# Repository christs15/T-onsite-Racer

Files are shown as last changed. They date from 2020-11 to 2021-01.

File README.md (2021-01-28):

# T-onsite-Racer 

Workshop Documentation for T-onsite Racer @ CMD+O



## Respository structure

**root directory:** Building instruction and programming instructions to build T-onsite-Racer.

**Groupwork**: Introdcution to Bluetooth Low Energy and Microcontroller.

**CAD::** T-Racer CAD Files.

**Arduino:** Template sketch as "programming guide" for the T-Racer and sample solution.

**App:** Link and introdcution to download the T-Racer app directly from AppStore/PlayStore to controll your car. For Android there is an prebuild apk. You can also find the source code of the app in the subdirectory "sources".

**images:** Pictures and impressions of the T-Racer.

## App

We have a prebuild IOS and Android app, which can be officially downloaded as a trial version in the respective stores. You can find the link to the app for your platform in the app subfolder.

You can also find the source code here. So you can build your app for the corresponding platform. The app is implemented in ionic and can be built for both, android and ios. First the development/build environment has to be configured accordingly:

1. Clone this repo
2. Install Node.js current version (https://nodejs.org/en/download/)
3. Install the Ionic CLI with npm in CMD - npm install -g @ionic/cli (https://ionicframework.com/docs/intro/cli)
4. Download Android SDK and JDK8 (https://ionicframework.com/docs/developing/android)
5. Download Gradle and set Path to System (https://gradle.org/install/)
6. Use IDE for modifications: example (Visual Studio Code - https://code.visualstudio.com/)
7. In project directory, install nippljs - npm i nipplejs (https://www.npmjs.com/package/nipplejs)

How to deploy on android device:
Note: Compatible with Android 5.2 and higher.

1. In project directory, run - ionic cordova prepare android (https://ionicframework.com/docs/cli/commands/cordova-prepare)
2.  In project directory, run - ionic cordova run android -1 (to deploy on android Phone: https://ionicframework.com/docs/cli/commands/cordova-run)

Visit "https://ionicframework.com/docs" for complete documentation.

## T-Racer "tuning"

To make the T-Racer a bit faster, you can buy a new engine, for example with 900rpm. Make sure that the dimensions are correct, otherwise it won't fit into the provided holder.

You can also turn up the step-up converter to 10-12V to get the maximum power out of your motor. 
Attention: The servo motor has an operating voltage of 5V. According to the wiring diagram, the servo is connected to the output of the step-up. If the step-up is turned up to over 5V, the servo must be replugged. You can then connect the servo motor directly to the battery.

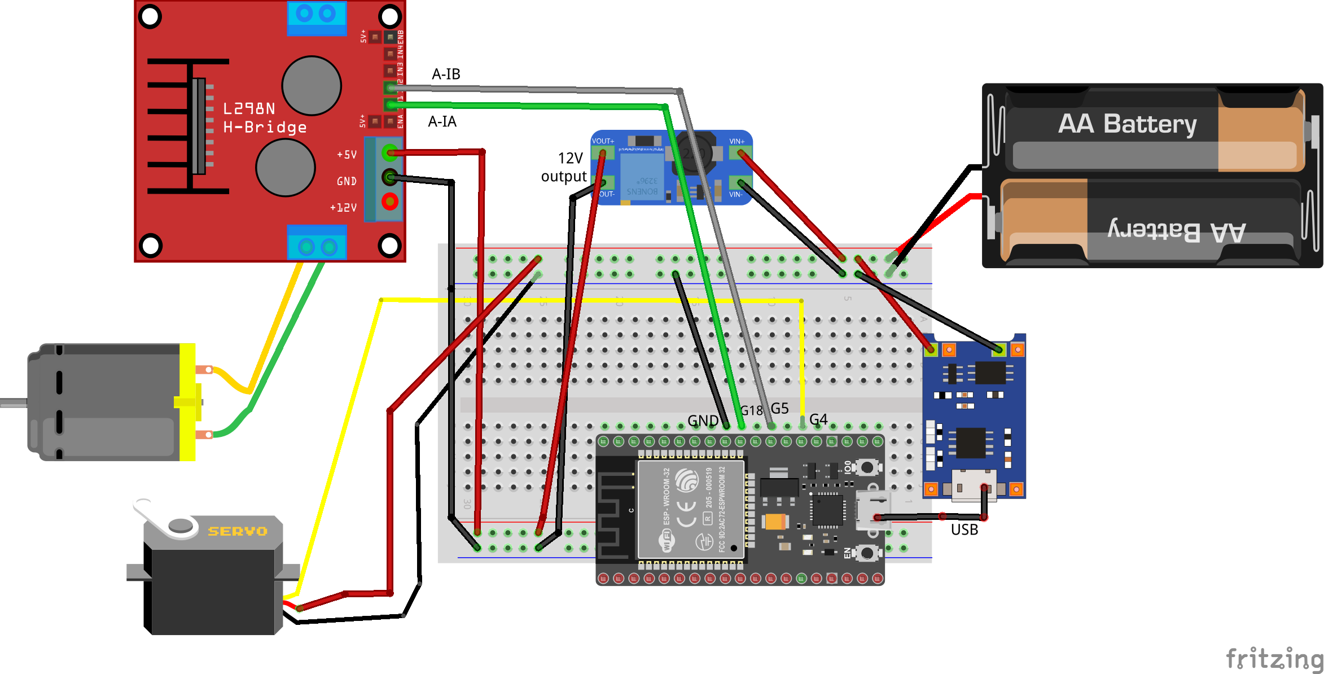
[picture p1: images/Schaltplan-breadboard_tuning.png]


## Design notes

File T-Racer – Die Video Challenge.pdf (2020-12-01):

# T-Racer – Die Video Challenge

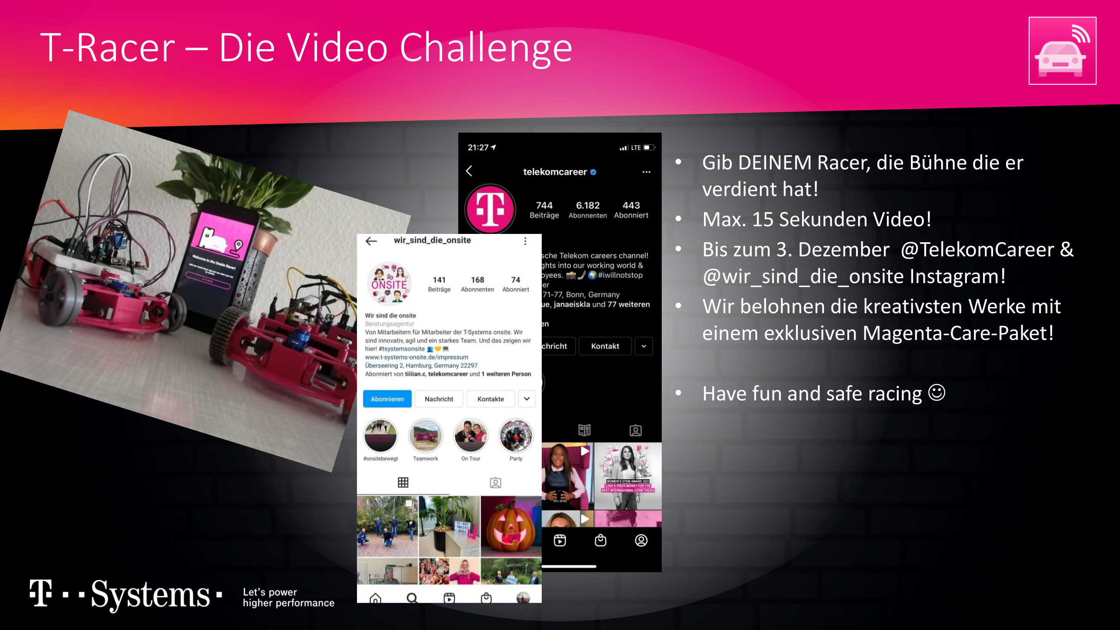
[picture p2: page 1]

- Gib DEINEM Racer, die Bühne die er verdient hat!
- Max. 15 Sekunden Video!
- Bis zum 3. Dezember @TelekomCareer & @wir_sind_die_onsite Instagram!
- Wir belohnen die kreativsten Werke mit einem exklusiven Magenta-Care-Paket!
- Have fun and safe racing ☺

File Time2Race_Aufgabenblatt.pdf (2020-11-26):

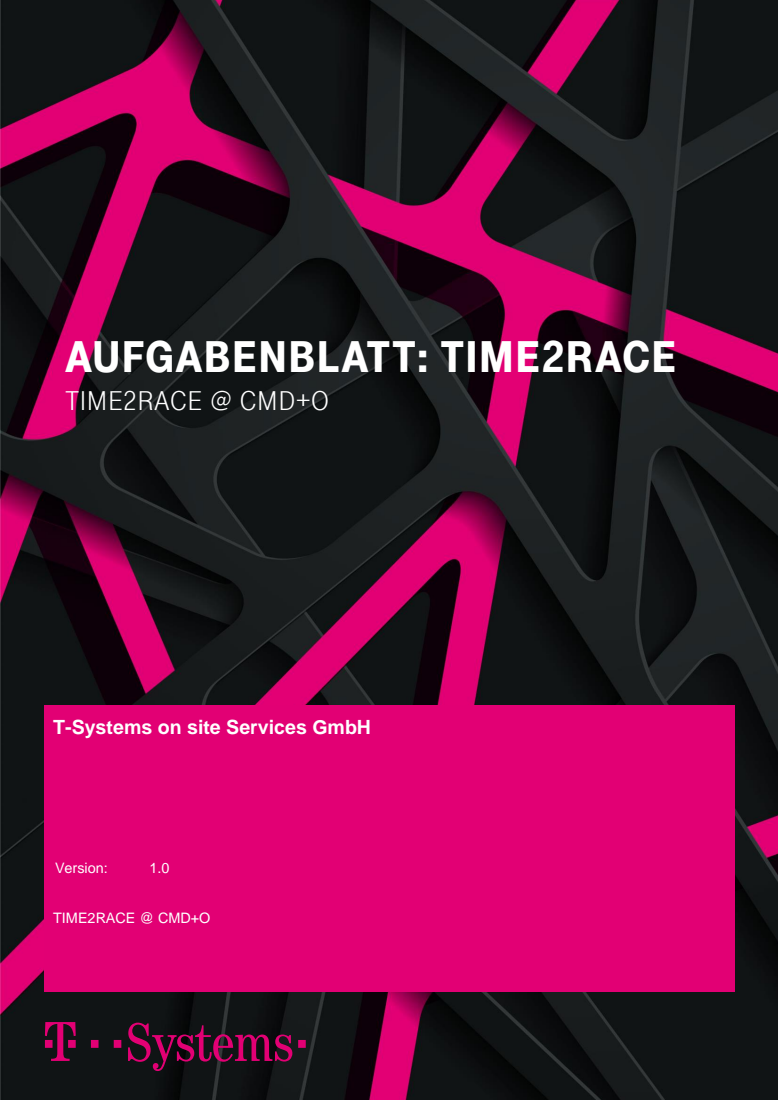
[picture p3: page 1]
AUFGABENBLATT: TIME2RACE; TIME2RACE @ CMD+O; Version:

T-Systems on site Services GmbH

T-SYSTEMS ON SITE SERVICES GMBH | Seite 2 von 20
Innovation Lab T-Systems onsite West | Version:1.0

TIME2RACE Aufgabenblatt

## IMPRESSUM

Herausgeber | T-Systems on site Services GmbH
| Fasanenweg 5 70771 Leinfelden-Echterdingen
Version | Letztes Review
1.00 | 20.11.2020

Kurzbeschreibung
Anweisung und Hilfestellung zur Umsetzung des T-Racers

Copyright © 20.11.2020 by T-Systems on site Services GmbH

Alle Rechte, auch die des auszugsweisen Nachdrucks, der fotomechanischen Wiedergabe (einschließlich Mikrokopie) sowie der Auswertung durch Datenbanken oder ähnliche Einrichtungen, vorbehalten.

## Inhaltsverzeichnis

## Abbildungsverzeichnis

1 | T-RACER
1.1 | Was ist zu tun?

Ziel dieses Workshops ist das Entwickeln deines eigenen T-Racers, welcher per Bluetooth Low Energy steuerbar ist. Das Herzstück des T-Racers ist ein ESP32 Dev Board, welches du über die Arduino IDE programmieren kannst. Darüber steuerst du den Motor für den Antrieb, sowie den Servo Motor für die Lenkung. Für die Kommunikation zwischen App und T-Racer wird das Protokoll Bluetooth Low Energy eingesetzt.

1.2 | Die Macht der Schaltung

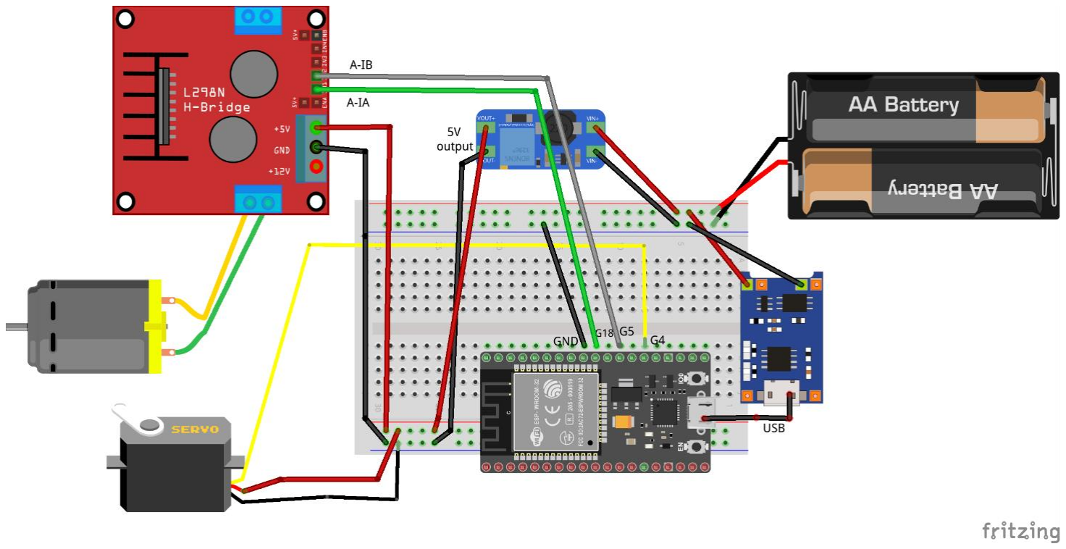
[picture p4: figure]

Abbildung 1: Schematischer Schaltplan

## 1.2.1 Hardware Komponenten

ESP 32

Step up (MT3608)

Der ESP32 ist eine kostengünstige und mit geringem Leistungsbedarf ausgeführte 32-Bit-Mikrocontrollerfamilie der Firma espressif. Er kommt standardmäßig mit Wifi und BLE an Bord.

Der MT3608 ist ein Step-Up Konverter (Auswärtswandler). Dieser wird benötigt, um die Spannung der Batterie auf konstante 5V zu regeln.

Eingangsspannung: 2V - 24V, Ausgangsspannung: bis 28V, Max Nennstrom: 2A

Power supply Modul

AA-Batterien

Servo Motor

DC Getriebe
Motor

L9110 Motor
controller

Breadboard

WICHTIG: Wenn der T-Racer nicht verwendet wird, sollte der Akku entfernt werden!

Wird benötigt, um die 4,5 Volt des Akkus auf konstante 5 Volt zu bringen, so kommt es nicht zu Verbindungsabbrüchen des BLE Chips. Der Spannungswandler verfügt über einen USB Output, wodurch eine einfache Stromversorgung des ESP32 ermöglicht wird.

3x 1,5V für die Stromversorgung

Servo Motor für die Lenkung des T-Racers.

DC Motor mit vorgeschaltener Getriebebox für den Antrieb. Durch die Getriebeübersetzung liefert der Motor genug Drehmoment, um den T-Racer zu bewegen. Max 300 rpm.

L9110 H-Bridge zum steuern des DC Motors. Mit dem L9110 können bis zu 2 Motoren angesteuert werden. Dieser ist erforderlich, um die Motorrichtung umkehren zu können. Mit einem einfachen MOS-FET können wir nur die Leistung ändern, aber nicht die Richtung.

Steckplatine für einfaches Prototyping.

2 | SETUP
2.1 | Ein Ausflug in die Bibliotheken

Um den Programmcode für unsere Christbaumkugel zu schreiben werden einige externe Bibliotheken benötigt, welche mittels „include“ eingebunden werden müssen.
Folgende Bibliotheken sind bereits durch Arduino selbst oder durch das „esp32“-Paket mitgeliefert:
- ESP_WiFi: (Optional) Stellt allgemeine Funktionen für WiFi-Verbindungen zu Verfügung. Wir benötigen
| sie aber nur um WiFi abzuschalten, damit der Stromverbrauch reduziert wird.
- BLEDevice: Klasse für ein BLE Device. Die Grundlage für die BLE Kommunikation.
- BLEServer: Klasse für einen BLE Server. Hierauf kann sich später das Smartphone verbinden.
- BLEUtils: Allgemeine Funktionen für BLE.
- ESP32Servo: Bibliothek für die Kommunikation mit dem Servo Motor
2.2 | Genau die richtige Debugging App für den T-Racer – nRFConnect

Um die Bluetooth-Verbindung von Smartphone aus zu testen kann die App nRFConnect genutzt werden. Die App ist für Android sowie iOS kostenlos verfügbar:
- https://play.google.com/store/apps/details?id=no.nordicsemi.android.mcp&hl=en_US
- https://apps.apple.com/us/app/nrf-connect/id1054362403
2.3 | Arduino - Was sonst?

Um das Board über euren Computer zu programmiere, müsst ihr es per Mikro-USB anschließen. Das Board wird über einen virtuellen COM Port angesprochen. Hierzu benötigt der Computer noch die passenden Treiber. Diese sind hier zu finden:
https://www.silabs.com/products/development-tools/software/usb-to-uart-bridge-vcp-drivers
Anschließend kann man sich die Arduino IDE unter https://www.arduino.cc/ für alle gängigen Betriebssysteme downloaden und installieren. Zunächst ist es wichtig, alle benötigten Boardkonfigurationen und Bibliotheken einzubinden, um den ESP32 über die IDE nutzen zu können. Dazu geht man unter „Datei -> Voreinstellungen“ und fügt eine „zusätzliche Boardverwalter-URL“ ein: https://dl.espressif.com/dl/package_esp32_index.json

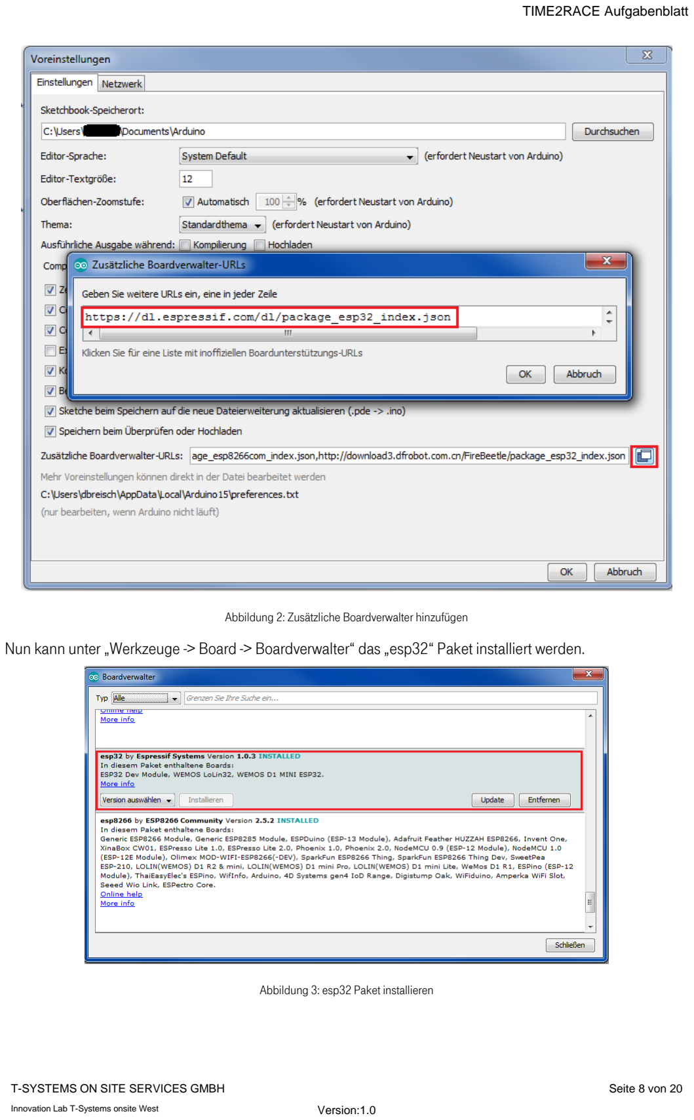
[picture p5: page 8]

Abbildung 2: Zusätzliche Boardverwalter hinzufügen
Nun kann unter „Werkzeuge -> Board -> Boardverwalter“ das „esp32“ Paket installiert werden.

Abbildung 3: esp32 Paket installieren

Damit nun die IDE weiß für welches Board tatsächlich entwickelt wird, gibt man abschließend unter „Werkzeuge“ die korrekte Konfiguration wie in Abbildung 4 dargestellt an. Wichtig hierbei ist zudem das Auswählen des richtigen virtuelle COM Ports, an dem das Board angeschlossen ist.

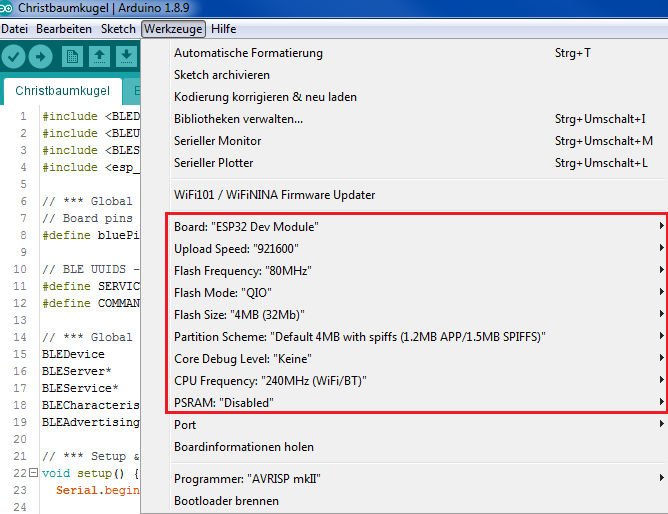
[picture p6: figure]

Abbildung 4: Boardkonfiguration
Will man den Sketch auf das Board flashen, klickt man auf den Pfeil „Hochladen“ (oben links in der IDE). Daraufhin wird der Sketch kompiliert und das Flashen beginnt. Will man lediglich kompilieren, klickt man auf den Haken „Überprüfen“.
Während des Flashvorgangs wird am unteren Bildschirm der aktuelle Vorgang in der Konsole ausgegeben. Sobald dort „Connecting…“ steht, muss in einigen Fällen der „Boot“ Knopf des Boards gedrückt werden, bis die Übertragung startet. Danach kann der Knopf losgelassen werden.

Abbildung 5: Konsolenausgabe beim Flashen
Eine praktische Debugmöglichkeit bietet der „Serielle Monitor“, der in der rechten oberen Ecke zu finden ist. Hier werden alle seriellen Ausgaben des Controllers angezeigt, die der Entwickler erstellt hat.

Abbildung 6: Button "Serieller Monitor"

Für Linux Nutzer:
Unter Linux muss zunächst die Versionskontrollsoftware Git und das Python-Modul Serial mittels

sudo apt install git python-serial

installiert werden.

Damit nun die IDE weiß für welches Board tatsächlich entwickelt wird, gibt man abschließend unter „Werkzeuge“ die korrekte Konfiguration wie in Abbildung 4 dargestellt an. Wichtig hierbei ist zudem das Auswählen des richtigen virtuelle COM Ports, an dem das Board angeschlossen ist.

2.4 | Sag Hallo, zur Welt!

Zum Testen der Konfiguration kann ein kleiner „Hello-World“ Sketch implementiert werden. Hierzu muss über „Datei -> Neu“ ein neuer Sketch angelegt werden. Mithilfe des in Abbildung 7 dargestelltem Sketch kann eine Serielle Ausgabe geschrieben werden, welche im Seriellen Monitor verfolgt werden kann. Dabei ist darauf zu achten, dass die Baudrate im Seriellen Monitor mit der im Sketch hinterlegten Baudrate (115200) übereinstimmt.

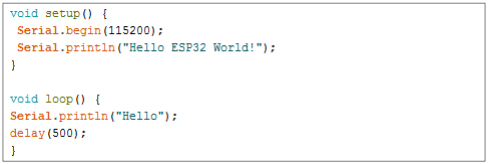
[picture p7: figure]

Abbildung 7 Hello World Sketch
2.5 | Warum löten, wenn man stecken kann?

Ein Breadboard (Steckplatine) ermöglicht es, schnell und einfach Schaltungen zu testen, ohne das gelötet werden muss.

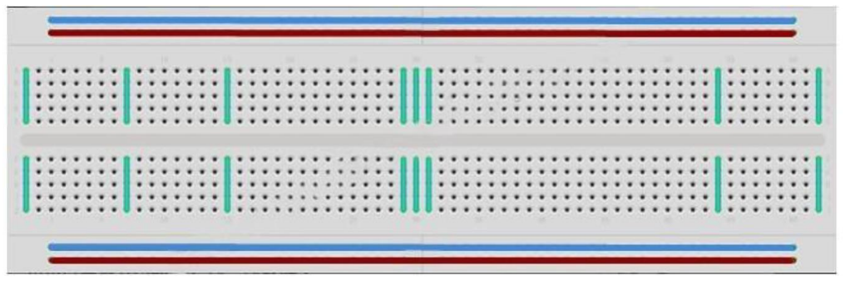
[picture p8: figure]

Abbildung 8 Breadboard

Innerhalb des Breadboards befinden sich Metallstreifen, welche die elektrische Verbindung zwischen den Kontaktstellen herstellen. Dabei sind immer die Kontakte innerhalb derselben Reihe (grün eingezeichnet) miteinander verbunden. Wenn du die Pins zweier Bauteile in dieselbe Kontaktreihe steckst, sind diese also miteinander verbunden. Zudem gibt es zwei „Powerlines“ (Rails), welche für die Stromversorgung genutzt werden.

3 | PROGRAM YOUR RACER
3.1 | Find the right way: Lenkung

Angeschlossen wird der Servo über ein dreipoliges Kabel. Dabei handelt es sich um zwei Versorgungsleitungen
- VCC (rot) und GND (braun), sowie eine Datenleitung (gelb).
Mit dem Servo wird eine Winkelbewegung zwischen 0 und 180 Grad gesteuert. Die Neutralposition ist dabei bei 90 Grad erreicht, während 0 und 180 Grad jeweils den Linken und Rechten Anschlag definieren. Bedeutet also, dass wenn du die Servo auf 90 Grad stellst, fährt dein T-Racer geradeaus.
Zur Ansteuerung des Servomotors werden wir die Servo-Klasse aus der Arduino-Servobibliothek " ESP32Servo.h " verwenden.

Beispiel:

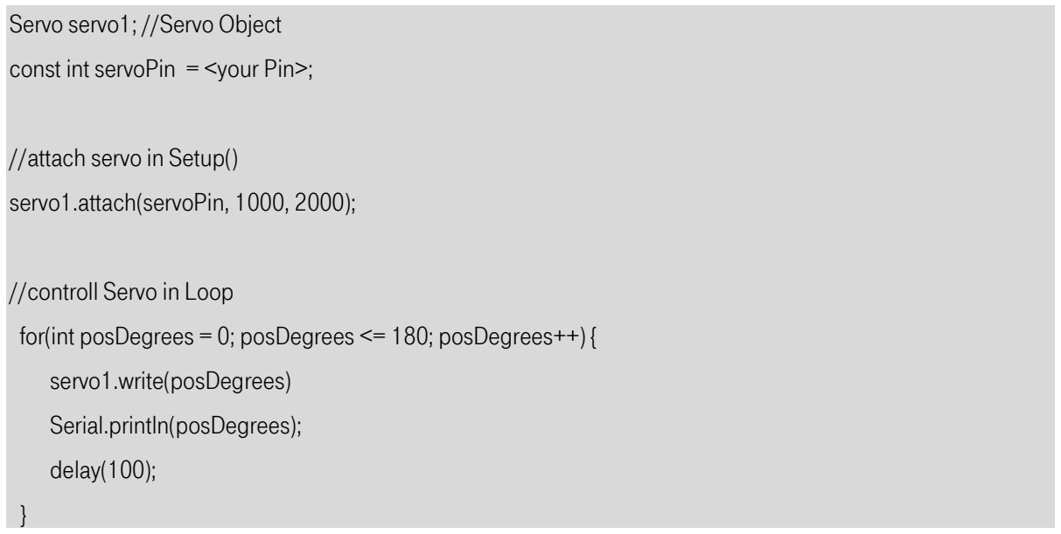
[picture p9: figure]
Servo servo1; //Servo Object; const int servoPin = <your Pin>;; //attach servo in Setup(); servo1.attach(servoPin, 1000, 2000);; //controll Servo in Loop; servo1.write(posDegrees); Serial.println(posDegrees);; delay(100);

for(int posDegrees = 0; posDegrees <= 180; posDegrees++) {

3.2 | Start your motors: Antrieb

Die digitalen Pins auf dem Entwicklerboard haben eine konstante Ausgangsspannung von 5V bzw. 3.3V. Um die Spannung ändern zu können, unterstützen einige Pins ein PWM-Signal.
Mit dem PWM-Signal und einem MOS-FET können wir die an einen Gleichstrommotor gelieferte Leistung variieren, um so die Geschwindigkeit zu bestimmen. Dadurch könnte die Leistung des Motors angepasst werden, allerdings kann so die Richtung nicht geändert werden. Um die Richtung zu ändern, muss die Polarität getauscht werden, hierzu wird die H-Bridge benötigt.
Motor Variablen definieren:
//motor Pins
int motorDir = 18; // → INA int motorPWM = 5; // → INB

MotorDIR: Richtung des Motors bestimmen (LOW oder HIGH) für Rückwerts oder Vorwärts.
MotorPWM: Drehzahl des Motors bestimmen (Geschwindigkeit) – LOW oder HIGH für volle Geschwindigkeit

Mithilfe der truth table, kann abgeleitet werden, wann der Motor rückwärts bzw. vorwärts fährt.

Table 1 truth table

IA | IB | Output
LO | LO | Off
HI | LO | Forward
LO | HI | Reverse
HI | HI | Off

Vorwärts:
- IA (motorDIR) auf HIGH setzen (5v)
- IB (motorPWM) 255 = Motor aus (siehe truth table), IB (motorPWM) 0 = volle Geschwindigkeit
- Die PWM-Zahl von IB kann nun angepasst werden, um die Leistung des Motors anzupassen → pow digitalWrite( motorDir, HIGH ); // direction = forward
analogWrite( motorPWM, pow );

Rückwärts:
- IA (motorDIR) auf LOW setzen (0v)
- IB (motorPWM) 0 = Motor aus (siehe truth table)
- IB = 255 = maximum power → pow digitalWrite( motorDir, LOW ); // direction = backwards analogWrite( motorPWM, pow );

Anhalten:
digitalWrite( motorDir, LOW ); // Set motor to off
digitalWrite( motorPWM, LOW );

Der Motor kann nun vorwärts und rückwärts betrieben werden indem jeweils die MotorDIR sowie der entsprechende PWM Wert (zwischen 0 und 255) gesetzt wird. Das heißt, wenn wir nur den Wert 0-255 senden, wissen wir nicht, ob der T-Racer vorwärts oder rückwärts fahren muss. Ein weiterer Wert, welcher diese Info enthält, müsste mitgesendet werden. Um dies zu umgehen, sendet die T-Racer App nur einen Wert von 0-255, wobei 128 Stillstand bedeutet. Ist der Wert größer als 128, sollte der T-Racer vorwärtsfahren, ist der Wert kleiner als 128, sollte der T-Racer rückwärtsfahren. Damit trotzdem das volle Spektrum des Motors genutzt werden kann, müssen die Werte entsprechend umgerechnet werden.

Vorwärts: pow = 255 - ((fb - 128) * 2);
Rückwärts: pow = 255 - (fb * 2);

Achtung: Wie rum du deinen Motor an der H-Bridge anschließt ist wichtig, um später beim Vorwärtsfahren, auch wirklich nach vorne zu fahren. Sollte dein Auto beim vorwärts Befehl, rückwärtsfahren, tausche einfach die Anschlüsse des Motors an der H-Bridge

3.3 | Connect to your T-Racer: BLE Verbindung initialisieren
1. Einbinden aller nötigen Bibliotheken
| Um die externen Bibliotheken nutzen zu können, müssen diese zu Beginn eingebunden werden.
| #include <BLEDevice.h> #include <BLEUtils.h> #include <BLEServer.h>
2. Variablen definieren
| Globale Variablen definieren:

…..
….
#define SERVICE_UUID "ae975c80-05f0-11ea-8d71-362b9e155667" #define COMMAND_CHAR_UUID "b81f189c-05f0-11ea-8d71-362b9e155667" BLEDevice Device;

BLEServer* pServer;
BLEService* pService;
BLECharacteristic* pControllCharacteristic; BLEAdvertising* pAdvertising;

setup{
….
….
}

loop{
…
….
}

Achtung: Achte darauf, dass die UUID´s übereinstimmen. Andernfalls kann die App deinen T-Racer nicht finden.

3. Bluetooth initialisieren
Um eine Verbindung mit dem Central einzugehen, muss zunächst das Bluetooth initialisiert werden. Dazu sind mehrere Schritte nötig.
a. Bluetooth Gerät erstellen
Zunächst muss das BLE Gerät initialisiert werden. Dabei kann der Name des Gerätes bestimmt werden.

Device.init("Name of BLE Device");

b. BLE Server erstellen
Nachdem das BLE Gerät erstellt wurde, muss dieses als BLE Server konfiguriert werden. pServer ist dabei vom Typ BLEServer:
pServer = Device.createServer();
c. Profil definieren

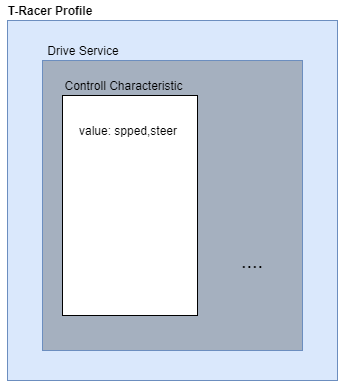
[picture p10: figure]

Abbildung 9 T-Racer Profile
void initBLE() {
….
…..
pService = pServer->createService(SERVICE_UUID);
pControllCharacteristic = pService->createCharacteristic(COMMAND_CHAR_UUID,
BLECharacteristic::PROPERTY_WRITE_NR | BLECharacteristic::PROPERTY_WRITE);
// has to be enabled for iOS pControllCharacteristic->setWriteNoResponseProperty(true);
//Callback Methoden
pServer->setCallbacks(new ServerCallbacks()); pControllCharacteristic ->setCallbacks(new CharacteristicCallbacks()); ….
…
}

d. UUIDs
Der Service sowie die Charakteristiken benötigen eine UUID, also eine einzigartige ID welche sie repräsentiert. Wie unter Aufgabenpunkt 2 werden dafür Präprozessor Konstanten angelegt. Diese werden direkt unter die oben angelegten Konstanten geschrieben. Damit BLE Client und BLE Server miteinander kommunizieren können, müssen beide das Profil implementieren. Der BLE Client (App) muss daher wissen in welche Charactersitic er die entsprechenden Werte schreiben muss. Um dies zu garantieren, müssen folgende UUIDs zugewiesen werden:

Drive ServiceUUID: "ae975c80-05f0-11ea-8d71-362b9e155667"
Controll CharacteristicUUID: "b81f189c-05f0-11ea-8d71-362b9e155667"
e. In den Advertising Zustand wechseln
Ist das Gerät initialisiert und das Profil definiert, kann der Service gestartet und in den Advertising Zustand gewechselt werden, sodass andere BLE Geräte das Gerät durch das Scannen der Umgebung finden können. Die nötigen Befehle können dem Cheat sheet entnommen werden. Anschließend versendet das Gerät Advertising Nachrichten mit der definierten Nachricht auf den dafür vorgesehen Advertising Kanälen. Durch das Scannen der Umgebung mithilfe der NRFConnect App, sollte das initialisierte Gerät nun sichtbar werden. Dazu muss der Sketch zunächst kompiliert und auf dem Mikrocontroller geflasht werden.
void initBLE {
…
…
//start_advertising
Device.startAdvertising(); Serial.println("Start Advertising"); }
3.4 | Control your T-Racer: Steuerung über BLE

Nachdem du dich erfolgreich mit deinem ESP32 verbinden kannst, wird es Zeit, die übertragenen Werte richtig zu empfangen und zu interpretieren.

1. Werte auf dem BLE-Server empfangen
Um den Wert der Charakteristik beim Empfangen eines neuen Wertes vom Client verarbeiten zu können, muss eine sogenannte Callback Methode definiert werden, welche aufgerufen wird, sobald ein Wert in die Charakteristik geschrieben wird.
Dazu muss zunächst die Callback initialisiert werden:

(Info: die Zeile habt ihr schon in der initBLE() Methode )

pCharCommand->setCallbacks(new CharacteristicCallbacks());

Anschließend kann über die Callback-Klasse der Wert ausgelesen werden, indem die Methode onWrite() überlagert wird.

class CharacteristicCallbacks: public BLECharacteristicCallbacks {
void onWrite(BLECharacteristic* pCharacteristic) {
//receive value via BLE from characteristic
std::string value = pCharacteristic->getValue();
//convert to String
String svalue= value.c_str();
}
};
2. Wert senden, empfangen und ausgeben
Um zu überprüfen, ob die gesendeten Werte richtig empfangen werden, eignet sich die App nRF Connect sehr gut. Damit kannst du dich mit deinem T-Racer verbinden und siehst anschließend das definierte BLE Profil.

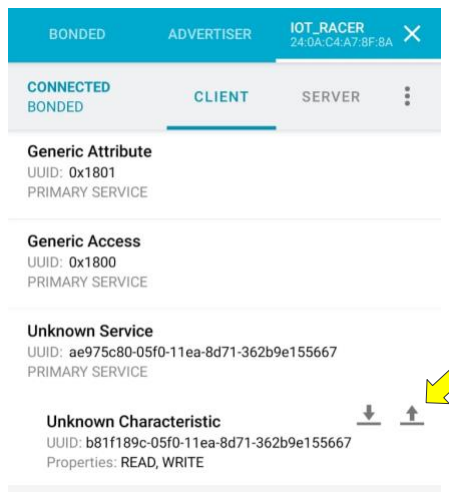
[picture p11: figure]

Um jetzt einen Wert zu senden, klicke auf den „write“-Pfeil und gebe einen Wert ein. Da serverseitig ein String erwartet wird, wähle UTF8 bzw. Text aus und klicke anschließend auf „send“. Danach solltest du den Wert im seriellen Monitor sehen können.

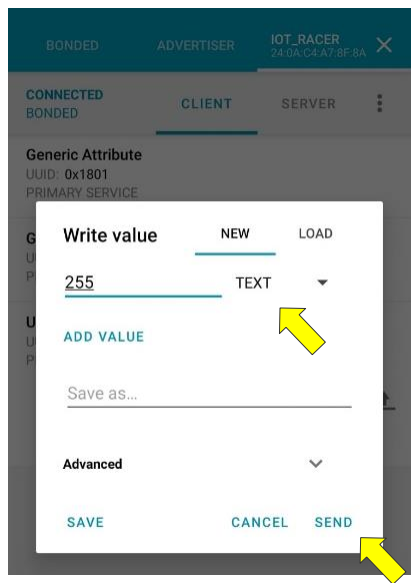
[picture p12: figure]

3. Werte interpretieren
Die T-Racer App sendet die Werte für die Lenkung und den Speed gebündelt in einer Charakteristik im folgenden Format: <speed,steer>
Daher müssen die Werte zuerst geparsed und dann an die Servo und den DC-Motor übergeben werden z. B über eine Methode carControll(speed, steer)

A | CHEATSHEET

Allgemein:

Serial.begin(9600) | Baudrate für die serielle Übertragung definieren.
Serial.println(“STRING“) Serial.print(“STRING“) | Gibt STRING auf dem seriellen Monitor aus. Ohne und mit Zeilenumbruch. Gut für Debugging.

Servo:

#include <ESP32Servo.h> | Include Servo Bibliothek

servo.attach(pin) | Servo dem entsprechenden Pin zuweisen.
- servo: eine Variable vom Typ Servo
- pin: Die Pin-Nr. welche der Servo zugewiesen werden soll
servo.write(angle) | Schreibt einen Wert und steuert die Welle entsprechend. Bei einem Standardservo wird dadurch der Winkel der Welle (in Grad) eingestellt und die Welle in diese Ausrichtung bewegt.
- Servo: eine Variable vom Typ Servo
- Winkel: der auf das Servo zu schreibende Wert, von 0 bis 18

DC Motor:

pinMode(motorDir,OUTPUT) pinMode(motorPWM,OUTPUT) | Configures the specified pin as input or output.
int pow = 255 - ((fb - 128) * 2) | Calculate the value when move forward
int pow = 255 - (fb * 2) | Calculate the value when move backward

Bluetooth Low Energy:
Dokumentation: https://github.com/nkolban/esp32-snippets/tree/master/Documentation

Device.init("T-Racer");
pServer = Device.createServer();
pService = pServer-> createService(SERVICE_UUID);

Erstellt ein BLE Device namens „T-Racer“, fügt einen Server sowie einen Service mit einer UUID hinzu.
Typ: BLEDevice
BLECharacteristic* pCharCommand;
BLEServer* pServer;

pCharCommand = pService-> createCharacteristic(COMMAND_CHAR_UUID, BLECharacteristic::PROPERTY_WRITE | BLECharacteristic::PROPERTY_WRITE_NR |
BLECharacteristic::PROPERTY_READ);

Erstellt eine Charakteristik für den Service pService. Parameter:
- COMMAND_CHAR_UUID:
Die UUID der Charakteristik.
- PROPERTY_WRITE: Die
Charakteristik hat
Schreibzugriff.
- PROPERTY_WRITE_NR:
Schreibzugriff ohne Response

BLEService* pService;

pService->start();

Startet den Service.

Device.init("T-Racer");
pServer = Device.createServer();
pService = pServer-> createService(SERVICE_UUID);

Erstellt ein BLE Device namens „T-Racer“, fügt einen Server sowie einen Service mit einer UUID hinzu.
Typ: BLEDevice
BLEAdvertising* pAdvertising;

pAdvertising = Device.getAdvertising(); pAdvertising-> addServiceUUID(SERVICE_UUID); pAdvertising->setScanResponse(true); pAdvertising->setMinPreferred(0x06); pAdvertising->setMinPreferred(0x12); Device.startAdvertising();

Konfiguriert und startet das BLE Advertising. Notwendig, um von anderen Geräten gesehen zu werden.

pServer->setCallbacks(new ServerCallbacks()); pCharCommand->setCallbacks(new CharacteristicCallbacks());

Callbacks für den Server und die Charakteristik registrieren. class ServerCallbacks : public BLEServerCallbacks {
void onConnect(BLEServer* pServerCallback) { Serial.println("Client connected");
}
};

Beispiel Server-Callback, der bei Verbindung eines Clients eine Meldung auf dem seriellen Monitor ausgibt.

class CharacteristicCallbacks : public BLECharacteristicCallbacks {
void onWrite(BLECharacteristic* pCharacteristic){
std::string value = pCharacteristic->getValue();
}
};

Beispielhafter Charakteristik Callback, welcher ein onWirte-event abfängt und den Wert ausliest.

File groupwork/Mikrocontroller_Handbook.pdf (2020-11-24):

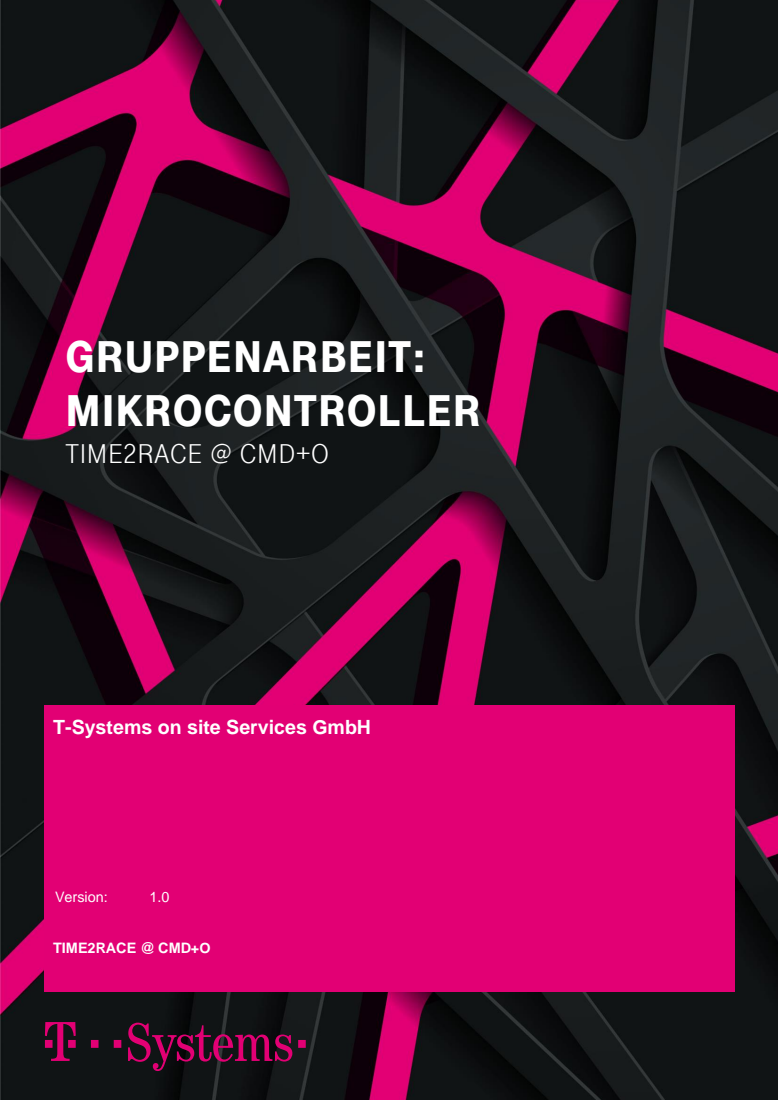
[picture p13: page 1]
GRUPPENARBEIT: MIKROCONTROLLER; TIME2RACE @ CMD+O; Version:

T-Systems on site Services GmbH

T-SYSTEMS ON SITE SERVICES GMBH | Seite 2 von 11
InnovationLab T-Systems onsite West | Version:1.0

Mikrocontroller

## IMPRESSUM

Tabelle 1 Impressum

Herausgeber | T-Systems onsite Services GmbH
| Fasanenweg 5
| 70771 Leinfelden-Echterdingen
Version | Letztes Review | Status
1.00 | 20.11.2020

Kurzbeschreibung

Grundlegende Informationen zur Programmierung von Microcontroller mithilfe der Arduino IDE sowie eine Anleitung zur Integration des ESP32 in die Arduino IDE.

Copyright © 20.11.2020 by T-Systems on site Services GmbH

Alle Rechte, auch die des auszugsweisen Nachdrucks, der fotomechanischen Wiedergabe (einschließlich Mikrokopie) sowie der Auswertung durch Datenbanken oder ähnliche Einrichtungen, vorbehalten.

## Inhaltsverzeichnis

## Abbildungsverzeichnis

1 | MIKROCONTROLLER

Einfach ausgedrückt handelt es sich bei einem Mikrocontroller um einen kleinen Computer, der kompakt auf einem Chip integriert ist (Ein-Chip-System oder System-on-a-Chip). Der Chip enthält einen Prozessor für die Ausführung von Programmen, verschiedene Arten von Speicher (Arbeits- und Programmspeicher) sowie Schnittstellen für die Kommunikation mit Peripheriegeräten (LEDs, Sensoren, usw.). Mikrocontroller sind in Leistung und Ausstattung auf die jeweilige Anwendung angepasst. Daher haben sie gegenüber „normalen“ Computern Vorteile bei den Kosten und der Leistungsaufnahme. Kleine Mikrocontroller sind in höheren Stückzahlen für wenige Cent verfügbar.
Einsatzbereiche von Mikrocontrollern sind meist in eingebetteten Systemen im Alltag, zum Beispiel in Kaffeemaschinen, Unterhaltungselektronik, Autos und Mobiltelefonen. Dort verrichten sie Steuerungsaufgaben anhand der Messwerte, die sie von ihren angeschlossenen Sensoren erhalten.
Bekannte Hersteller von Mikrocontrollern sind z.B.: Atmel, Intel oder Samsung. Die Programmierung erfolgt meist in den Programmiersprachen C oder Assembler.

2 | ARDUINO
2.1 | Arduino Plattform

Arduino ist eine Open-Source Elektronik Plattform, die aus einem Hardware- und Softwareteil besteht. Dadurch soll jedem interessierten die Möglichkeit gegeben werden auf dieser Basis Anpassungen für eigene Projekte zu erstellen und zu verwenden. Ziel ist es, einer breiteren Masse einen einfachen Zugang zu Elektronik zu ermöglichen. Die Webpräsenz ist zu finden unter www.arduino.cc. (https://telekom-my.sharepoint.de/personal/christian_pitters_t-systems_com/Documents/Allgemein_Office/IoT_Workshop/Workshop_Dokumente/www.arduino.cc)

2.2 | Arduino Hardware

Arduino bietet eine breite Palette an vorgefertigten Entwicklerboards an, die direkt für eigene Projekte eingesetzt werden können. Für verschiedene Anwendungsgebiete sind spezielle Boardfamilien verfügbar, zu den bekanntesten zählt der Arduino Uno. Zudem sind für viele Boards die Layouts und Produktionsdateien unter Creative Commons freigegeben. Dadurch sind mittlerweile diverse Arduino kompatiblen Boards von Drittherstellern oder Privatpersonen entstanden.
Die meisten Arduino Boards basieren auf Atmel Mikrocontrollern, die um verschiedene Speicher, Schnittstellen und Funktionen erweitert sind, je nach Modell. Die Controller sind mit einem Bootloader vorprogrammiert, der das Uploaden von eigenem Code über eine USB-Schnittstelle ermöglicht.
Beispielhafter Aufbau eines original Arduino Boards:

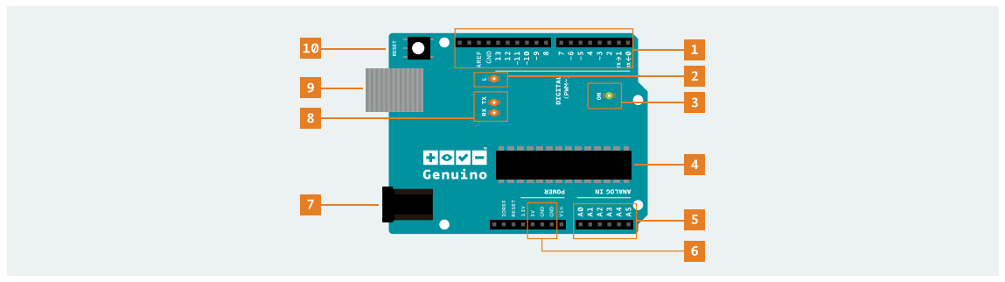
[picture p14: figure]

Abbildung 1: Aufbau eines Genuino Boards
1. Digital Pins: Können als Ein- und Ausgangspins für Peripherie genutzt werden.
2. Pin 13 LED: Einzige OnBoard-LED, kann z.B. für Debugging genutzt werden.
3. Power LED: Zeigt an ob der Arduino mit Strom versorgt wird.
4. ATmega Mikrocontroller: Das Herz des Boards.
5. Analog In: Analoge Eingangspins für Signale von z.B. Sensoren.
6. GND und 5V Pins: Anschlusspins, um Peripherie mit Strom über den Arduino zu versorgen.
7. Stromanschluss: Kann genutzt werden, um den Arduino mit Strom zu versorgen, wenn er nicht gerade per USB angeschlossen ist.
8. TX und RX LEDs: Werden genutzt, um die Kommunikation des Bords mit dem Computer anzuzeigen, z.B. beim Uploaden eines Programms.
9. USB Port: Wird genutzt, um den Arduino mit Strom zu versorgen, ein Programm hochzuladen oder über serieller Kommunikation zu debuggen.
10. Reset Button: Resettet den ATmega Mikrocontroller.

2.3 | Arduino IDE

Neben den Hardwareboards bietet Arduino auch eine eigene IDE für die Entwicklung eigener Programme an. Die Arduino IDE wurde mit Java entwickelt und ist kostenlos für Windows, macOS und Linux verfügbar. Die Programmierung selbst erfolgt in einer C bzw. C++-ähnlichen Programmiersprache, wobei technische Details wie Header-Dateien vor den Anwendern weitgehend verborgen werden und umfangreiche Bibliotheken und Beispiele die Programmierung vereinfachen.
Bibliotheken und Boardkonfigurationen - welche zum Entwickeln auf unterschiedlicher Hardware nötig sind -lassen sich einfach über einen eigenen Dienst im Hintergrund herunterladen und aktualisieren, der IDE muss hierzu lediglich eine URL zum Downloadserver zur Verfügung gestellt werden. Viele dieser Bibliotheken werden von den Hardwareherstellern oder der Open Source Community kostenlos angeboten.
2.4 | Struktur

Der grundlegende Aufbau der Arduino Programmiersprache ist relativ einfach und teilt sich in mindestens zwei Teile auf. Diese zwei benötigten Teile oder Funktionen umschließen Blöcke von Anweisungen.
void setup()
{
setupAnweisungen();
}

void loop()
{
anweisungen();
}
Hierbei ist setup() die Vorbereitung und loop() ist die Ausführung. Beide Funktionen sind notwendig damit das Programm ausgeführt werden kann. Die Setup Funktion sollte der Variablen Definition folgen, die noch davor aufgeführt werden muss. Setup muss als erste Funktion in einem Programm durchlaufen werden. Sie wird nur einmal ausgeführt und dient beispielsweise dem Setzen von PinMode oder der Initiierung der seriellen Kommunikation.
Nach der setup() Funktion folgt die loop() Funktion. Sie beinhaltet Programmcode, der kontinuierlich in einer unendlichen Schleife ausgeführt wird - Eingänge auslesen, Ausgänge triggern, etc. Diese Funktion ist der Kern von allen Arduino Programmen und erledigt die Hauptarbeit.
2.5 | Serielle Kommunikation

Serial.begin(rate);
'Serial.begin(rate)' Öffnet den seriellen Port und setzt die Baud Rate (Datenrate) für die serielle Übertragung fest. Die typische Baud Rate mit dem Computer ist 9600 Baud. Andere Geschwindigkeiten werden jedoch auch unterstützt.

void setup() {
Serial.begin(9600); | //öffnetseriellen Port // setzt die Datenrate auf 9600 bps

}
Serial.println(data) Schreibt Daten zum seriellen Port, gefolgt von einem automatischen Zeilenumbruch als Carrier Return und Linefeed. Dieser Befehl hat dieselbe Form wie 'Serial.print()', ist aber einfacher auf dem seriellen Monitor zu lesen.
Serial.println(analogValue); // sendet den Wert von 'analogValue'
Das folgende einfache Beispiel liest einen Wert vom analogen Pin 0 aus und sendet die Daten an den Computer einmal pro Sekunde.
void setup() {
Serial.begin(9600); // setzt die Datenrate auf 9600 bps
}
void loop() {
Serial.println(analogRead(0)); // sendet den Analogwert delay(1000); // pausiert fuer 1 Sekunde
}

3 | ESP32
3.1 | Chipvorstellung

Der ESP32 Chip ist ein kostengünstiger Mikrocontroller der Firma espressif, der besonders auf geringen Stromverbrauch ausgelegt ist. Sein besonderes Merkmal ist die direkte Integration von WLAN und Bluetooth Low Energy, was ihn im Moment auf dem Markt besonders auszeichnet. Andere Mikrocontroller bieten dies in der Regel nur über Hardwareerweiterungen durch sogenannte „Shields“ an.
Meist wird der ESP32 in verschiedenen Varianten von espressif selbst, aber auch von diversen Drittherstellern auf einem Entwicklungsboard zur Verfügung gestellt. Diese Boards unterscheiden sich untereinander zum Teil stark in der Anzahl und Belegung der Anschlusspins, sowie den technischen Spezifikationen, wie Stromverbrauch und unterstütze Schnittstellen sowie dem Preis.
Die Programmierung des ESP32 kann mit Hilfe verschiedener Plattformen wie Arduino oder MicroPython erfolgen. espressif bietet zudem ein eigenes Framework namens Espressif IoT Development Framework an. Weiterführende Links:
- https://www.espressif.com/en/products/hardware/esp32/overview
- https://docs.espressif.com/projects/esp-idf/en/latest/

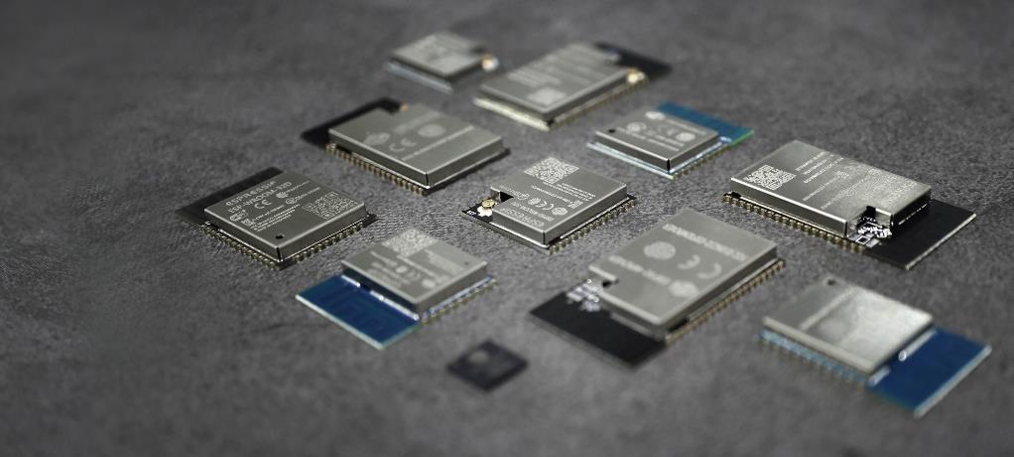
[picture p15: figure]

Abbildung 2: Verschiedene ESP32 Chips

3.2 | ESP32-DevKitC

Für unseren Workshop nutzen wir das gängige Entwicklungsboard „ESP32-DevKitC“ vom Dritthersteller AZ-Delivery, welches ein klein wenig anders aufgebaut ist als das offizielle Modell von espressif:

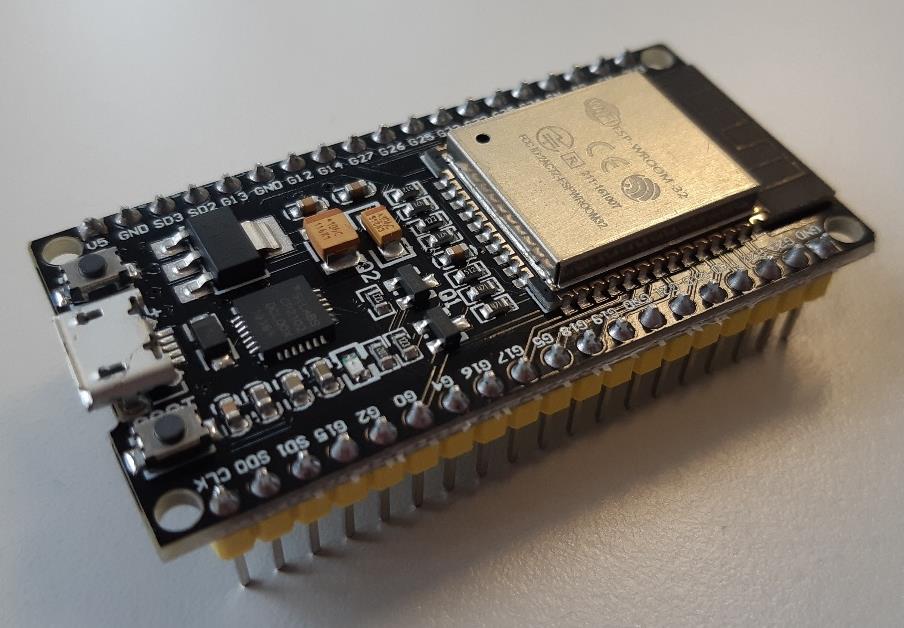
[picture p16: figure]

Abbildung 3: ESP32-DevKitC
Das Board verfügt über eine CPU mit 2 Tensilica-LX6-Kernen, getaktet mit bis zu 240 MHz, und 512 Kilobyte SRAM. Dazu integriert er eine Funkeinheit für WLAN (nach 802.11bgn) und Bluetooth (Classic und LE).
Die WLAN-Funktion unterstützt alle gängigen Verschlüsselungsmethoden, wie zum Beispiel WPA2. Außerdem kann er im WLAN auch als Access Point oder Sniffer agieren. Über 32 GPIO-Pins stehen unter anderem UART, I2C, SPI, DAC, ADC (12 Bit) zur Verfügung, alle GPIO-Pins können als Ein- oder Ausgabe benutzt werden. Weiterführende Links:
- https://www.espressif.com/en/products/hardware/esp32-devkitc/overview
- https://docs.espressif.com/projects/esp-idf/en/latest/hw-reference/get-started-devkitc.html

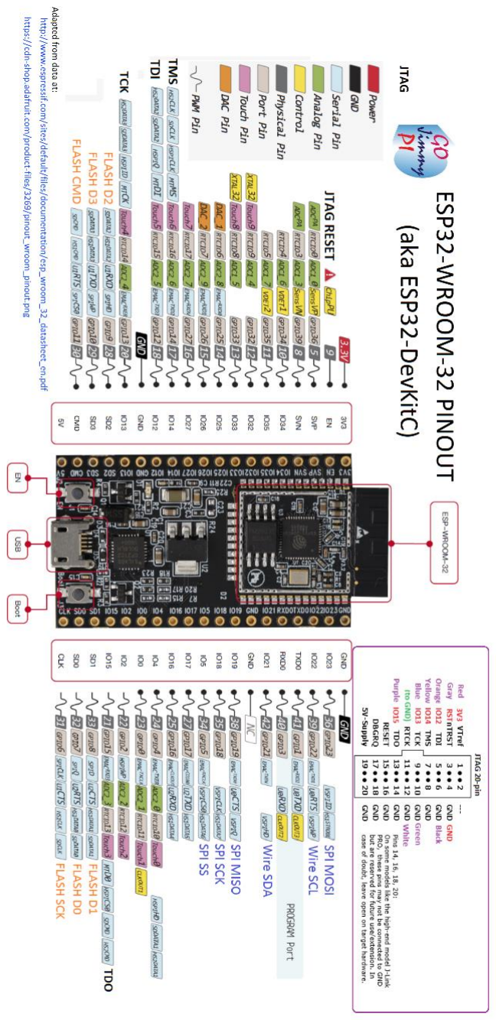
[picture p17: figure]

Abbildung 4: Pinout ESP32-DevKitC

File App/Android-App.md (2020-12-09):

Link to download public test version of T-onsite Racer Android App from google play store:

https://play.google.com/store/apps/details?id=de.tsystems.onsite

Or search for t-onsite racer in playstore.

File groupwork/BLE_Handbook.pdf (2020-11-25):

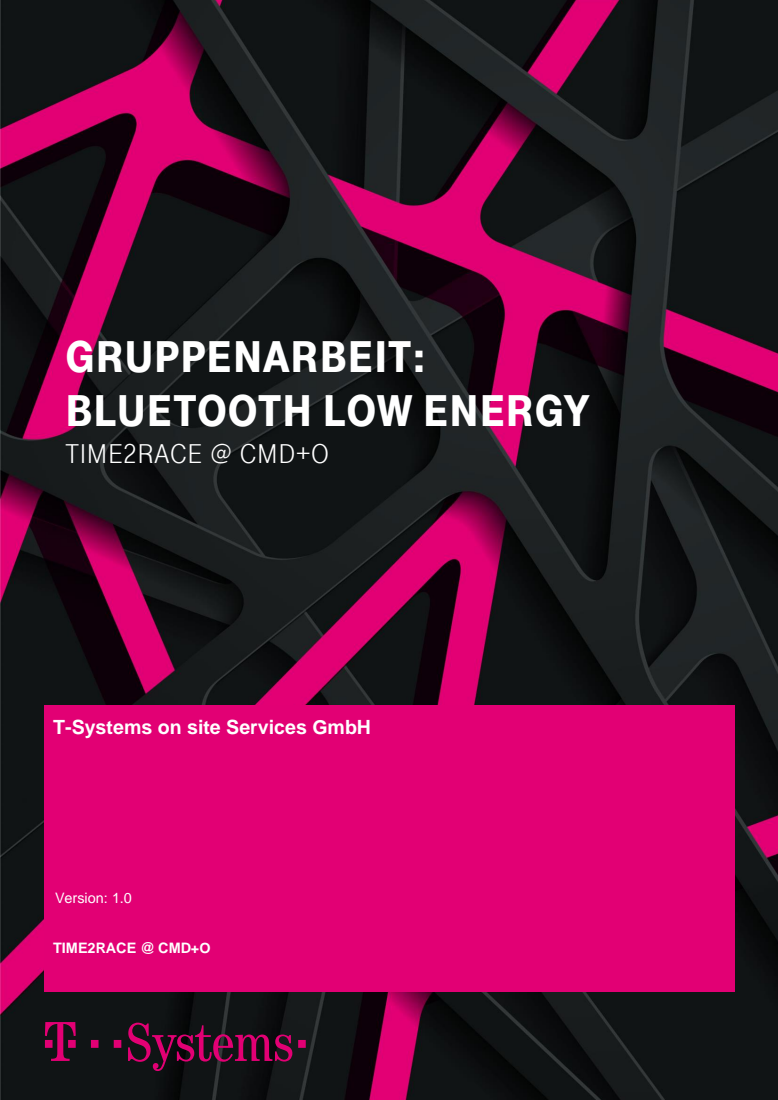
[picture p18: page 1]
Version: 1.0; TIME2RACE @ CMD+O

GRUPPENARBEIT:
BLUETOOTH LOW ENERGY
TIME2RACE @ CMD+O

T-Systems on site Services GmbH

T-SYSTEMS ON SITE SERVICES GMBH | Seite 2 von 9
InnovationLab T-Systems onsite West | Version:1.0

Bluetooth Low Energy

## IMPRESSUM

Tabelle 1 Impressum

Herausgeber | T-Systems onsite Services GmbH
| Fasanenweg 5
| 70771 Leinfelden-Echterdingen
Version | Letztes Review | Status
1.00 | 20.11.2020

Kurzbeschreibung

Grundlegende Informationen zu Bluetooth Low Energy sowie zum Aufbau und der Funktionsweise, als Vorbereitung für die Umsetzung des T-Racers

Copyright © 20.11.2020 by T-Systems on site Services GmbH

Alle Rechte, auch die des auszugsweisen Nachdrucks, der fotomechanischen Wiedergabe (einschließlich Mikrokopie) sowie der Auswertung durch Datenbanken oder ähnliche Einrichtungen, vorbehalten.

## Tabellenverzeichnis

## Abbildungsverzeichnis

1 | WAS IST BLUETOOTH/LOW ENERGY

Bluetooth ist ein internationaler Standard, mit dem Geräte über eine Funkverbindung kommunizieren können. Es ist bestens für die Kurzstrecken Übertragung geeignet und zudem sehr günstig zu Erwerben.
Hintergrund der Entwicklung war, die seriellen Kabel beim Datenaustausch zwischen zwei oder mehreren Geräten zu ersetzen und die Vernetzung mehrerer Geräte somit flexibler und einfacher zu machen. Über die Jahre hinweg, ist der Anwendungsbereich der Bluetooth Technologie jedoch enorm gewachsen und bietet mittlerweile viele Anwendungsmöglichkeiten. Heutzutage ist Bluetooth weit verbreitet, so gut wie jedes Notebook, Handy oder Tablet besitzt Bluetooth. Außerdem wird es oft in Lautsprechern, Headsets, Kameras oder Peripheriegeräten Geräten wie Maus und Tastatur eingesetzt.
Um den Einsatz auch in mobilen Geräten, die nur mit einem kleinen Akku betrieben werden, zu gewährleisten, wurde die Erweiterung Bluetooth Low Energy der Bluetooth Spezifikation 4.0 hinzugefügt. Wie der Name schon sagt, wurde hier das Ziel eines geringen Stromverbrauchs verfolgt. Dadurch können Geräte, die nur mit einer kleinen Knopfbatterie betrieben werden, mehrere Monate oder Jahre ohne aufladen aushalten.
1.1 | Ein Blick zurück

Bluetooth entstand 1994 durch eine Machbarkeitsstudie des Unternehmens Ericsson, in der sie versuchten eine alternative zu entwickeln, um Handys mit Handy-Zubehör ohne Kabel zu verbinden. Es sollte eine Funktechnik entwickelt werden, mit der die Kommunikation von Geräten ohne direkten Sichtkontakt möglich ist. Schon früh spielte "low-power" und "low-cost" eine entscheidende Rolle. Ericsson merkte auch, dass ein offener Standard benötigt wird, damit sich die Technik erfolgreich auf dem Markt etabliert. Da die Studie erfolgreiche Ergebnisse lieferte, verbündeten sich 1998 die Unternehmen Ericsson, Intel, IBM, Nokia und Toshiba und gründeten die Bluetooth SIG, um die Entwicklung einer offenen Spezifikation voranzutreiben (Bluetooth Special Interest Group).
Die Arbeiten an der Funktechnik starteten unter dem Namen "Multi-Communicator Link". Mit der Gründung der Bluetooth SIG wurde der Name „Bluetooth“ offiziell für die Funktechnik angenommen. Das Wort Bluetooth wurde dabei in Anlehnung an den dänischen Wikinger und König Harald Blåtand (eng. Bluetooth) gewählt. Dieser lebte im zehnten Jahrhundert und Vereinigte Dänemark und Norwegen. Möglicherweise war diese Tat ausschlaggebend für die Benennungen der Technologie. Genau wie Harald Blatand, will Bluetooth Sachen miteinander "vereinen" bzw. zusammenschließen, um miteinander zu kommunizieren.
Ein Jahr darauf, 1999, veröffentlichte die Bluetooth SIG die erste Version der Bluetooth Spezifikation. Daraufhin folgten weitere Versionen, die einen immer größeren Datendurchsatz und eine immer höhere Geschwindigkeit zum Ziel hatten.
Bluetooth Low Energy kam als Teil der Bluetooth Spezifikation 4.0 im Jahr 2010, wodurch sich die Ziele grundlegend verändert haben. Bei BLE wurde dahingegen eine radikale Änderung vorgenommen. Hauptziel dabei ist, so energiesparend wie möglich zu arbeiten. Der Datendurchsatz spielt dabei keine entscheidende Rolle. Der eigentliche Anwendungsfall besteht darin kleine Daten zu übertragen, und zwar nur dann, wenn sie gebraucht werden. Das bedeutet allerdings auch, dass einige Kernkomponenten von Bluetooth neu entworfen wurden und sich BLE somit in einigen Aspekten anders verhält wie das Klassische Bluetooth. 2016 veröffentlichte die Bluetooth SIG die momentan aktuelle Version 5.

1.2 | Kompatibilität von Bluetooth und Bluetooth Low Energy

Heutzutage gibt es eine Vielzahl an unterschiedlichen Bluetooth Geräten mit vielen verschiedenen Versionen von vielen verschiedenen Herstellern von Bluetooth. Damit diese reibungslos miteinander kommunizieren können ist die Abwärtskompatibilität eine grundlegende Voraussetzung. Grundsätzlich sind alle Bluetooth Versionen abwärtskompatibel. Zusatzfunktionalitäten wie High Speed (HS) oder Enhanced Data Rate (DER) sind jedoch nicht Abwärtskompatibel und können nicht zusammen mit einer älteren Version genutzt werden.
Mit der Einführung von BLE entstand jedoch eine neue Klassifizierung von Bluetooth. BLE unterscheidet sich in vielen wichtigen Aspekten und auch im Protokoll Stack. Demnach muss man heute zwischen Klassischem Bluetooth und Bluetooth Low Energy unterscheiden. Unter Klassischen Bluetooth versteht man Bluetooth bis zur Version 4.0, also die Art von Bluetooth die für großen Datendurchsatz gedacht ist (Basic Rate und Enhanced Data Rate). Die andere Klassifizierung ist Bluetooth low Energy, Energiesparend ohne das Ziel große Datenmengen zu übertragen. Ein Gerät kann allerdings Klassisches Bluetooth, Bluetooth low Energy oder beides unterstützen. Diese Klassifikationen nennt man dann classic-, Single- oder Dual Mode oder auch Smart und Smart Ready.

Tabelle 2 Kompatibilität zwischen Singel-, Dual-, und Classic Mode

| Singel Mode | Dual Mode | Classic Mode
Singel Mode | JA | JA | NEIN
Dual Mode | JA | JA | JA
Classic Mode | NEIN | JA | JA
1.3 | Einsatzgebiete

Bluetooth ist mittlerweile eine etablierte Funktechnik und in jedem Smartphone und vielen andren Geräten wie Lautsprecher und Notebooks verbaut. Allerdings muss man bei den Einsatzgebieten zwischen klassischem Bluetooth und Bluetooth Low Energy unterscheiden, da sich BLE in vielen Aspekten anders verhält und es aufgrund des geringeren Datendurchsatzes für andere Anwendungsfälle gedacht ist. Dadurch, dass bei BLE das Hauptmerkmal auf den geringen Stromverbrauch gelegt wurde, bietet sich der Einsatz für smarte mobile Anwendungen, meist mit einem geringen Datendurchsatz an.
Bei der Entwicklung ging es nicht darum Bluetooth zu optimieren, sondern einen neuen Markt für Bluetooth zu erschließen. Dadurch hat sich eine Reihe von neuen Einsatzmöglichkeiten für Bluetooth eröffnet. In den verschiedensten Bereichen, wie im Gesundheitsbereich, im Fitnessbereich, für die Indoor Navigation und auch im Bereich Smart Home kann und wird BLE eingesetzt. Dabei geht es um die Übertragung von kleinen Datenmengen von kleinen Geräten mit wenig Energiekapazität. Die Nutzung liegt demnach meist im mobilen Bereich, mit dem Ziel, so wenig Energie wie möglich zu verbrauchen.

2 | BLE PROTOKOLL STACK

Bluetooth Low Energy unterscheidet sich in vielen Punkten von classic Bluetooth. Der Protokoll Stack muss vielen neuen Anforderungen gerecht werden, wie zum Beispiel das Energiesparende Arbeiten oder die Kostengünstige Produktion. Um diese Anforderungen zu erfüllen, wurde der Protokoll Stack von BLE komplett überarbeitet. Einige Schichten wurden behalten, jedoch angepasst, andere wurden komplett entfernt oder durch neue ersetzt. Aus diesem Grund ist Bluetooth Low Energy nicht kompatibel mit den vorherigen Bluetooth
Spezifikationen, | wodurch | vermehrt | Dual-Mode | Geräte | zum | Einsatz | kommen.

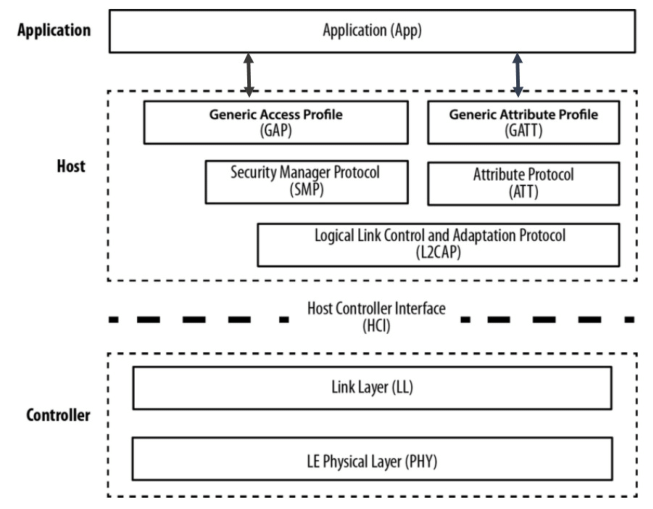
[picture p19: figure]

Abbildung 1 Bluetooth Low Energy Protokoll Stack
2.1 | Zustandsautomat

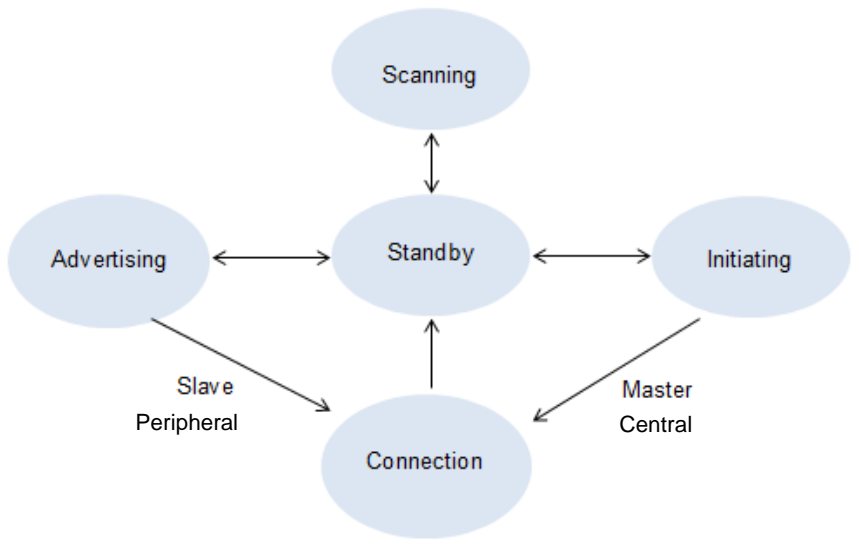
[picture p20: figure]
Peripheral; Central

Standby: Dies ist der Anfangszustand eines BLE Geräts. In diesem Zustand sind Empfänger und Sender geschlossen und der Energieverbrauch ist sehr gering. Erst wenn vom Host Layer eine Anweisung kommt etwas zu tun, wird der Zustand gewechselt.
Advertising: In diesem Zustand sendet ein BLE Gerät sogenannte Advertising Nachrichten, auf den dafür vorhergesehenen Advertising Kanälen. Dadurch können andere Geräte in der Umgebung das sendende Gerät finden.
Scanning: In diesem Zustand scannt ein BLE Gerät die Advertising Kanäle und lauscht nach Advertising Nachrichten. So können Geräte in der Umgebung gefunden werden.
Initiating: Wenn der Scanner entscheidet eine Verbindung aufzubauen, wechselt er in den Standby Zustand und direkt danach in den Initiating Zustand, um ein Connection Request an den Advertiser zu senden. Danach wechselt der in den Connection Status mit der Rolle Master bzw. Central, in der Annahme, dass der Advertiser dasselbe tut (als Slave).
Connection: In diesem Zustand ist ein Gerät verbunden. Es kann diesen Zustand vom Initiating oder vom Advertising Zustand erreichen. Beim Wechsel vom Initiating Zustand in den connection Zustand, wird ihm die Rolle „Master“ zugeteilt, ansonsten die Rolle „Slave“. Die Rollennamen unterscheiden sich allerdings auf den jeweiligen Schichten.
2.2 | Senden

Bluetooth Low Energy nutzt das 2.4GHz ISM Band. Dieses steht weltweit unlizenziert zur Verfügung. Das bedeutet, jeder darf auf dieser Frequenz senden, ohne Gebühren dafür zu bezahlen. Allerdings muss man sich dabei auch an ein paar sehr detailreiche Regeln halten. Grob zusammengefasst sagen diese, dass das 2.4GHz ISM Band nur für PANs und LANs mit einer limitierten Sendeleistung und Reichweite genutzt werden darf. Da das 2.4Ghz Band weltweit unlizenziert zu Verfügung steht, nutzen auch viele weitere Funktechnologien wie z.B. WLAN oder ZigBee diese Frequenz.

2.3 | Gerät finden

Damit BLE Geräte sich gegenseitig finden können, definiert die BLE Spezifikation Advertiser und Scanner. Der Advertiser sendet dabei jeweils eine Advertising Nachrichten auf jedem der drei Advertising Kanäle, während ein Scanner diese Kanäle abhört. Dieser Vorgang wird als Advertising Event bezeichnet.

2.4 | Verbinden

Um eine Verbindung aufzunehmen, muss der Scanner mit einem Connection Request auf ein Advertising Event antworten. Dieses Paket enthält alle Informationen, die für einen Verbindungsaufbau notwendig sind.

3 | PROFILE

Profile werden von der Anwendung zur Datenkommunikation zwischen zwei angeschlossenen Geräten verwendet.
Wie zwei Geräte via BLE miteinander kommunizieren, wird über das so genannte Generic Attribute Profile (GATT) definiert. Auf den Peripherals läuft dazu jeweils ein GATT-Server, auf dem Central ein entsprechender GATT-Client. Sprich: Wenn sich ein Smartphone mit mehreren E-Health-Geräten verbindet, läuft auf jedem dieser Peripherals ein GATT-Server, auf dem Smartphone dagegen jeweils ein GATT-Client. Welche Daten von einem GATT-Server bereitgestellt werden, wird über so genannte Profile definiert. Dabei handelt es sich um eine Zusammenstellung verschiedener Services, die von dem jeweiligen Peripheral zur Verfügung gestellt werden. Ein Profil ist ein Zusammenschluss aus einem oder vielen verschiedenen Services. Alle Profile basieren Dabei auf GATT. Die Bluetooth SIG stellt bereits einen fertigen Satz von BLE Profilen zur Verfügung. Mit diesen lassen sich einige Anwendungsfälle abdecken. Allerdings haben Entwickler auch die Möglichkeit eigene Profile, basierend auf GATT, zu entwerfen, um neue Anwendungsfälle abzudecken.

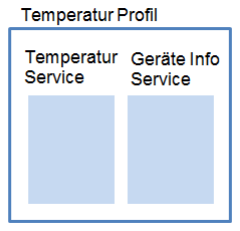
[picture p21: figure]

Abbildung 2 Profil kapselt mehrere Services

3.1 | Service

GATT verwendet das Attribut-Protokoll ("Attribut-Protokoll (ATT)") als Transportprotokoll, um Daten zwischen Geräten auszutauschen. Diese Daten sind hierarchisch in Abschnitten organisiert, die Services genannt werden und konzeptionell zusammenhängende Teile von Benutzerdaten, die Charakteristiken genannt werden, gruppieren. Ein Service ist also einfach gesagt, eine Sammlung von vielen Charakteristiken.

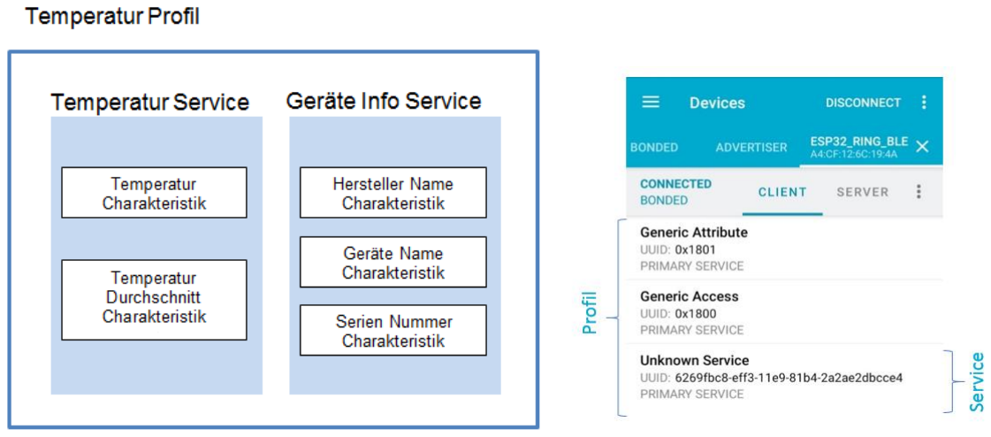
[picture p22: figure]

Abbildung 3 Darstellung der Service in nRF Connect | Abbildung 4 Ein Service kapselt verschiedene Charakteristiken
3.2 | Charakteristik

Eine Charakteristik ist ein Wert innerhalb eines Services, wie zum Beispiel die aktuelle Temperatur oder der aktuelle Akkustand. Dabei wäre allerdings z.B. die aktuelle Temperatur nicht sehr aussagekräftig, da die Einheit (°C, °F, …) und die Art der Temperatur (außen Temperatur, innen Temperatur, …) unbekannt sind Deshalb wird jede Charakteristik durch eine Charakteristik Definition definiert.

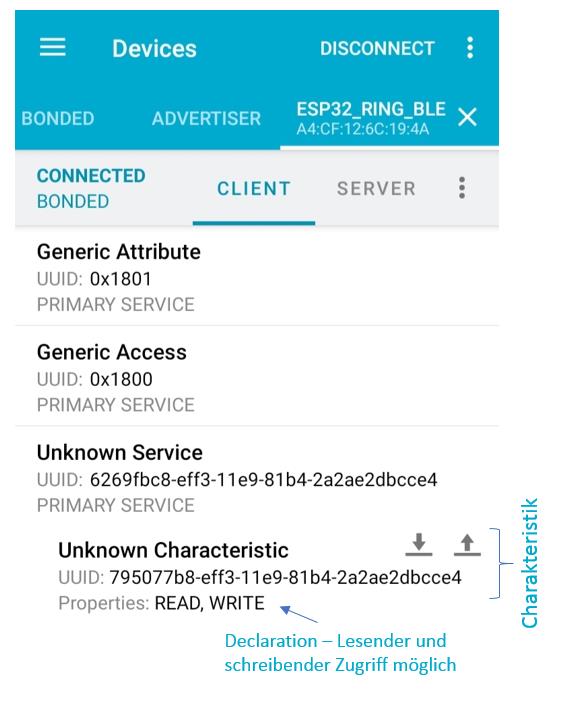
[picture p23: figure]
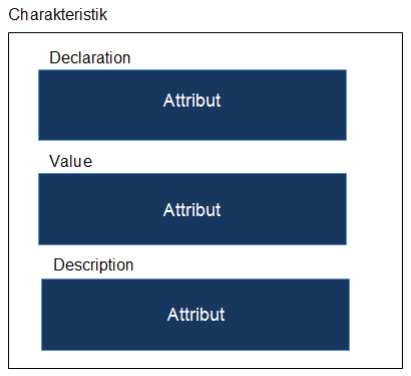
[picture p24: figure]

Abbildung 5 Darstellung einer Charakteristik in der nRF Connect App Abbildung 6 Aufbau einer Charakteristik

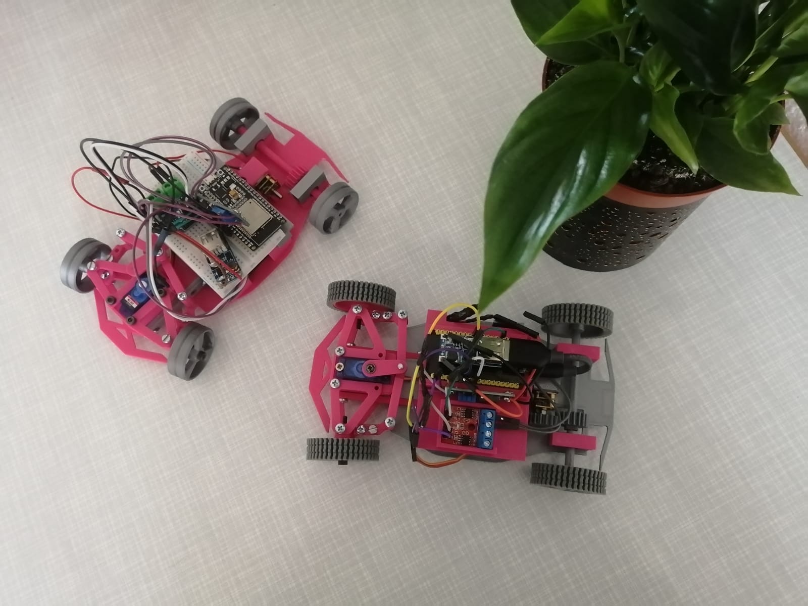
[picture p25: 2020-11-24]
images/T-Racer2.jpg

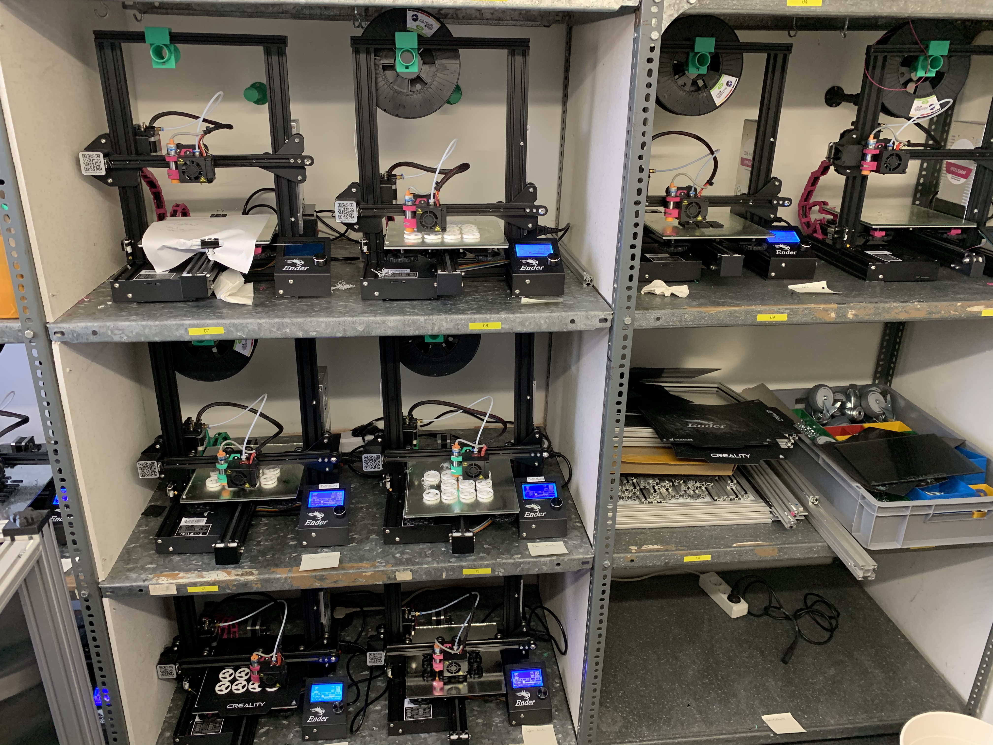
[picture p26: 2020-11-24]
images/Druck2.jpeg

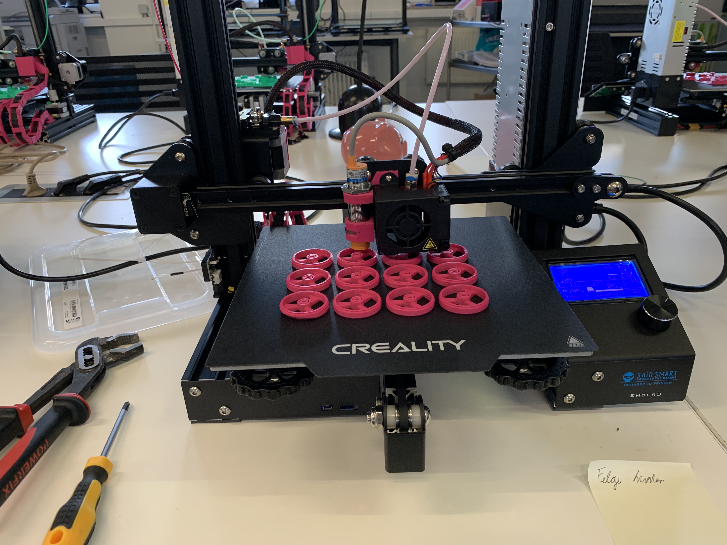
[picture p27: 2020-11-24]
images/Druck1.jpeg

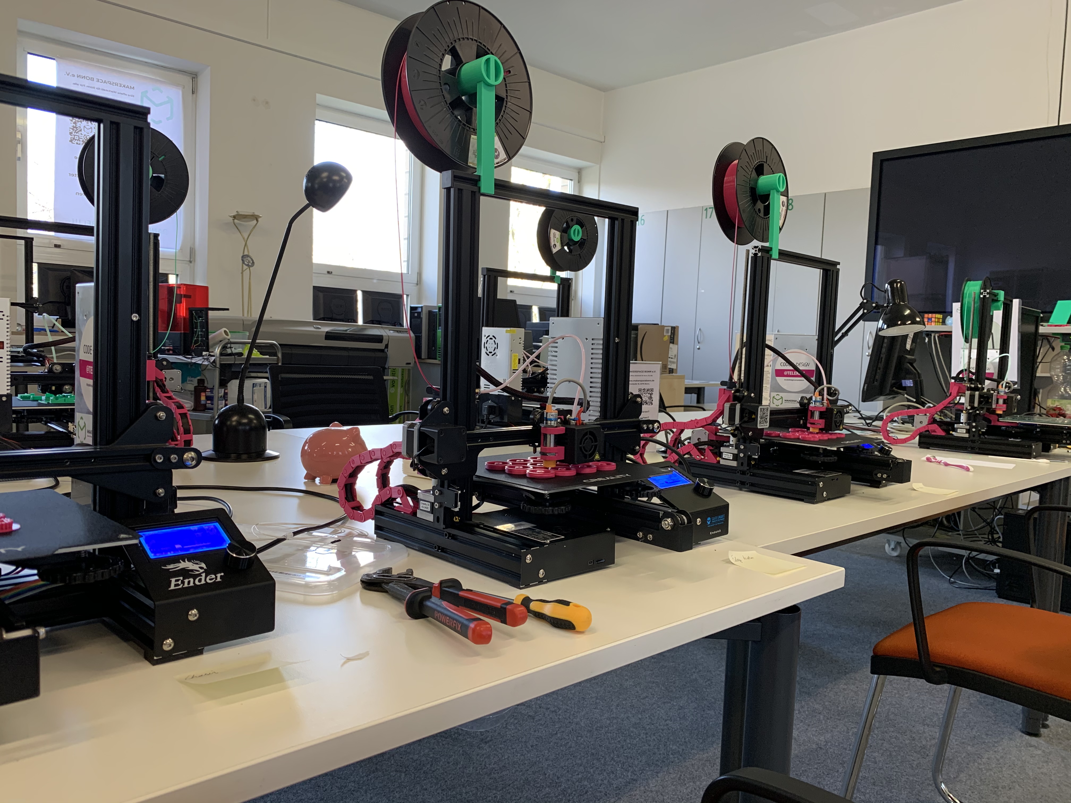
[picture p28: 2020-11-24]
images/Druck3.jpeg

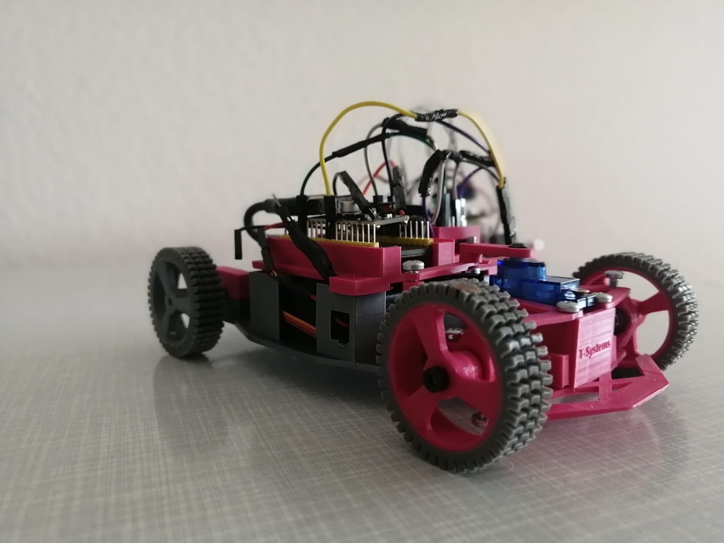
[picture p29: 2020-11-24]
images/T-Racer1.jpg

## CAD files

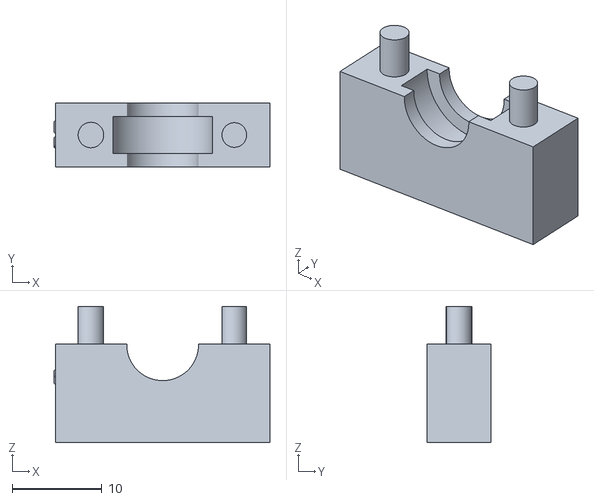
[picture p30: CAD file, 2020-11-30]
CAD/hinterachse-anbautile-2x.stl
24.1 x 7.12 x 15.2

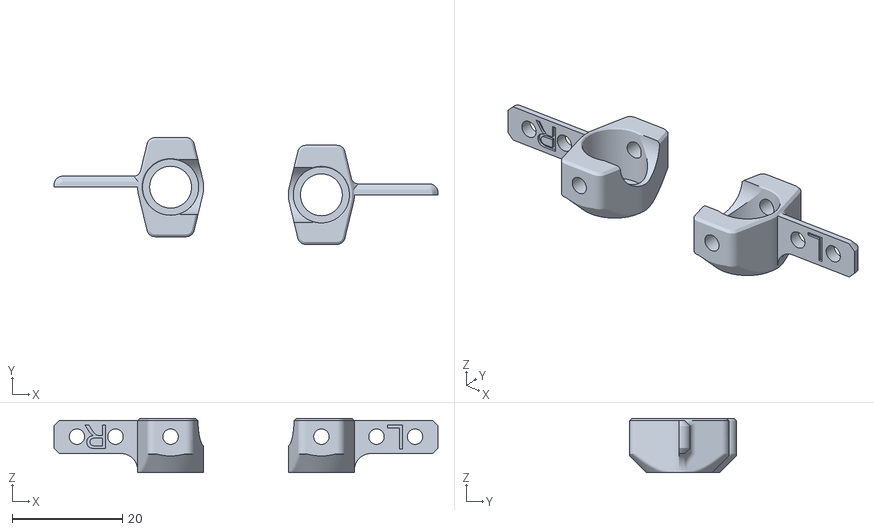
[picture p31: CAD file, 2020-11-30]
CAD/Vorderachse_Radlager-1x.stl
69.7 x 19.4 x 9.80

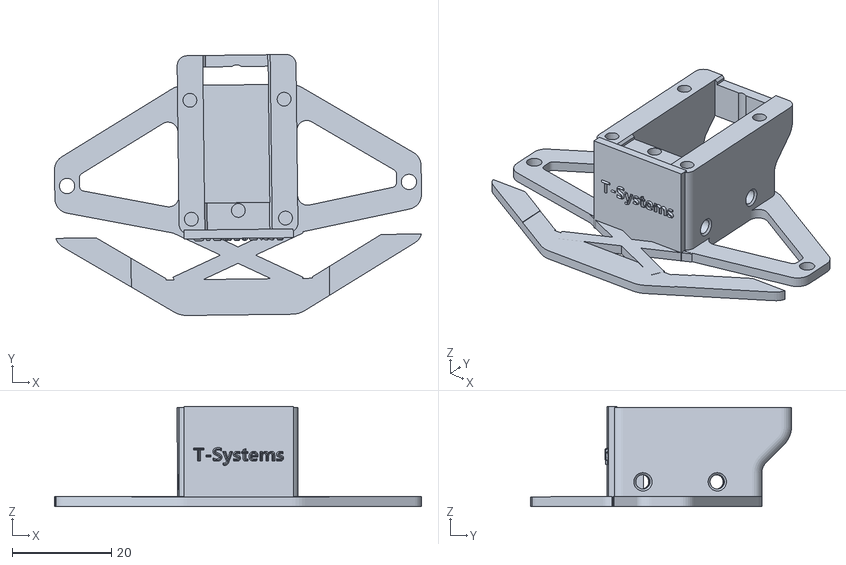
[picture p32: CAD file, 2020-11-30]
CAD/Vorderachse_servoHalterung-1x.stl
74.1 x 52.7 x 20.2

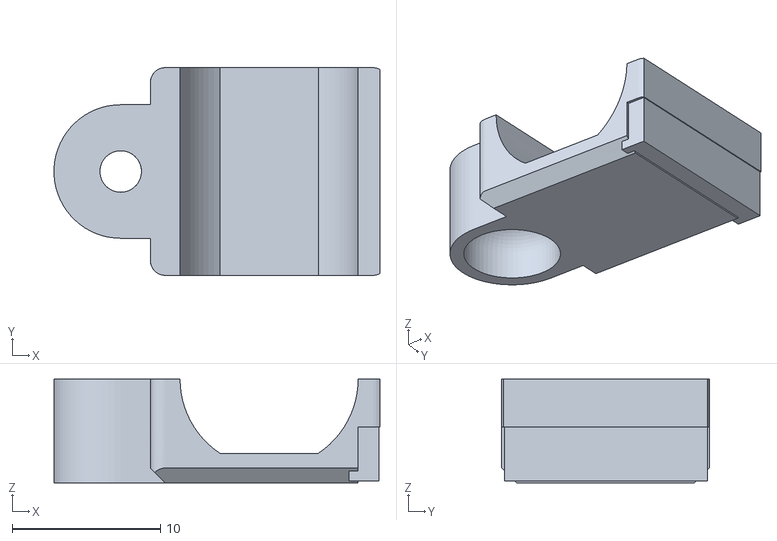
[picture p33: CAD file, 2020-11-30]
CAD/motorhalterung-1x.stl
22.0 x 14.0 x 7.00

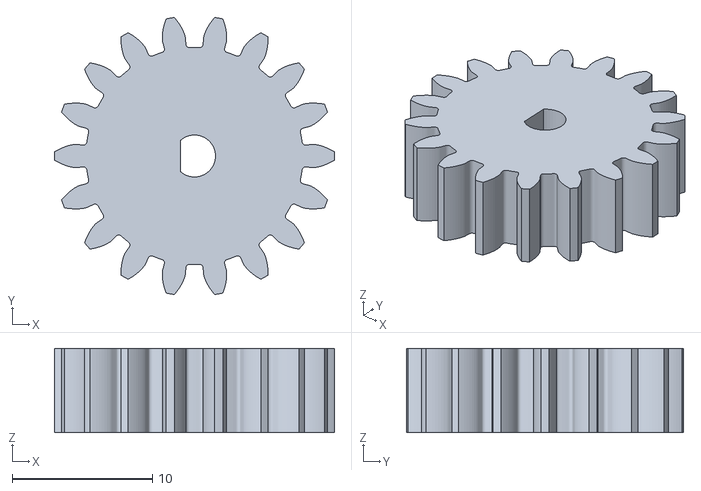
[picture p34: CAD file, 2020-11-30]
CAD/zahnrad_motor-1x.stl
20.0 x 19.8 x 6.00

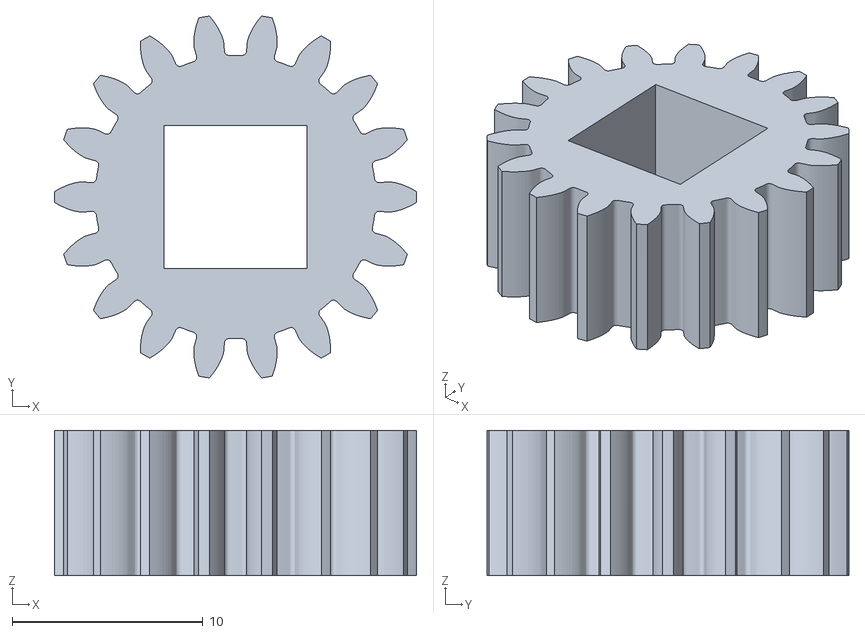
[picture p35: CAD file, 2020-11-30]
CAD/zahnrad_hinterachse-1x.stl
19.0 x 19.0 x 7.61

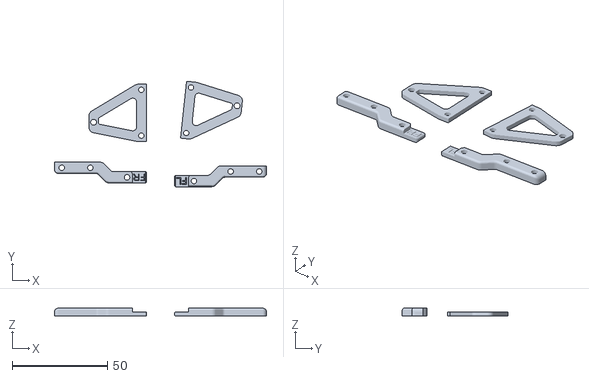
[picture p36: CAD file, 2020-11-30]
CAD/Vorderachse_anbauteile-1x.stl
111.1 x 55.3 x 4.00

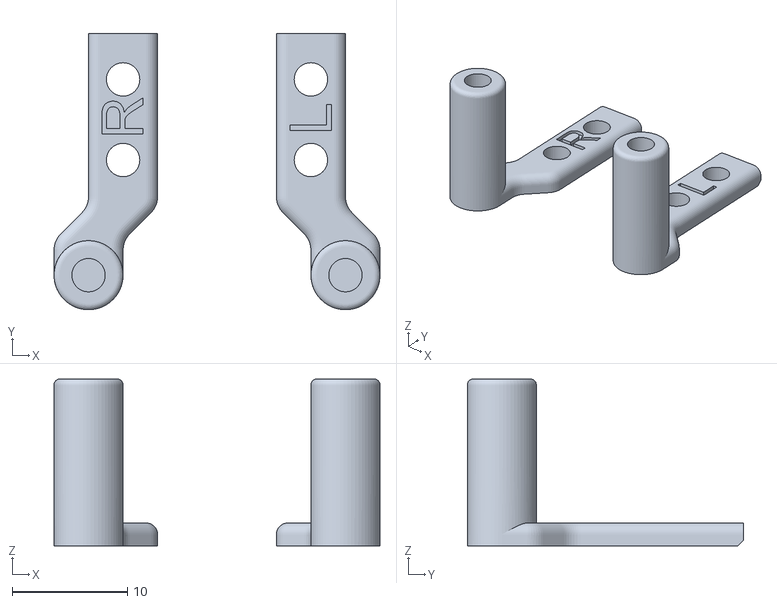
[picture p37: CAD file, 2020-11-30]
CAD/Vorderachse-achstraeger-1x.stl
28.3 x 24.0 x 14.5

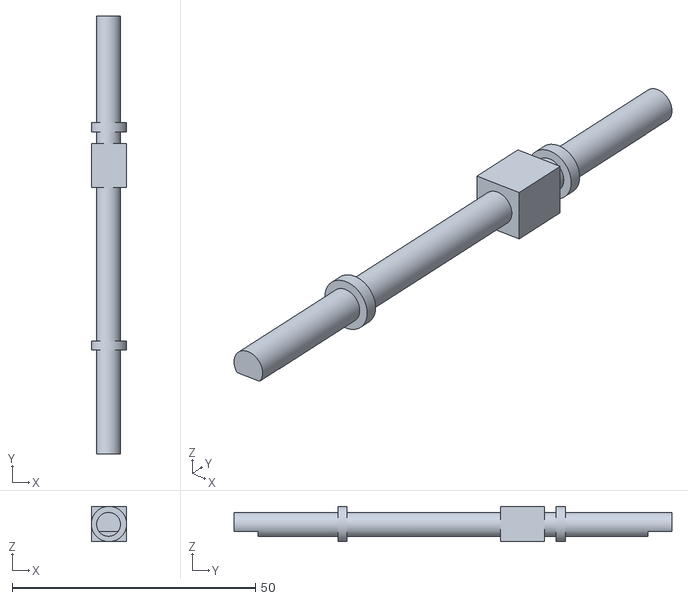
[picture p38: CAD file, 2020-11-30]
CAD/hinterachse-1x.stl
7.25 x 90.0 x 7.25

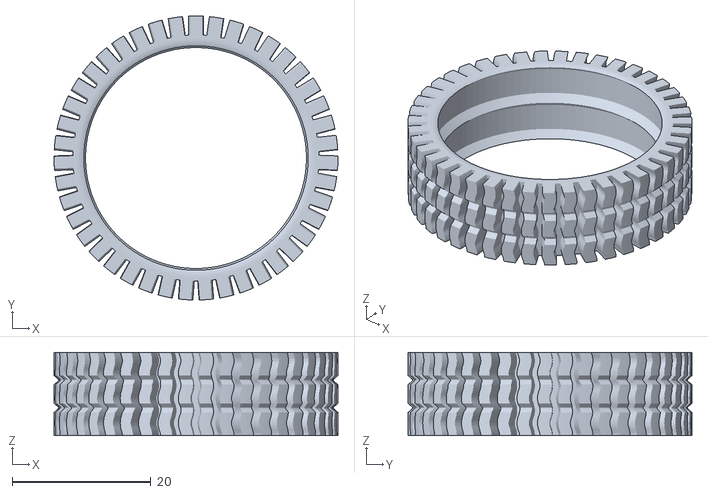
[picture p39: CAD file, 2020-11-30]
CAD/tire-TPU_x4.stl
41.0 x 41.0 x 12.0

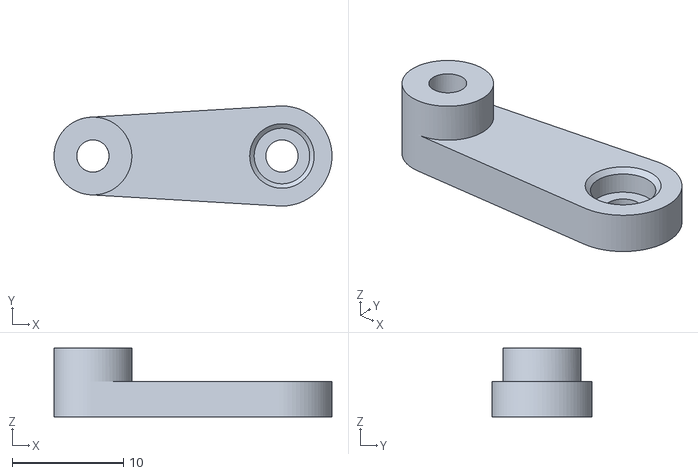
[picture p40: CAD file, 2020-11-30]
CAD/Vorderachse_servoarm-1x.stl
25.0 x 9.00 x 6.20

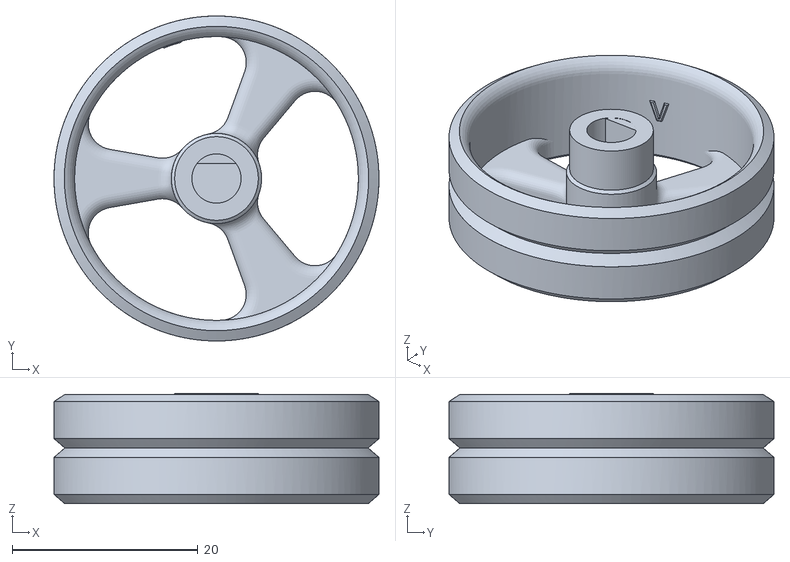
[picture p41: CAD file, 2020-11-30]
CAD/Felgen_heck-2x.stl
35.0 x 35.0 x 11.9

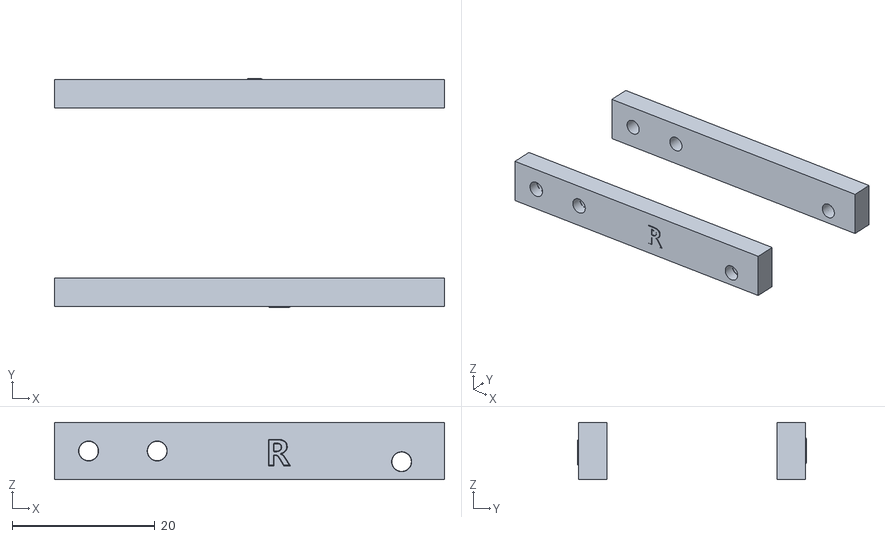
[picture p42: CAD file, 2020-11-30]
CAD/Verbindung-Vorderachse_1x.stl
54.6 x 32.0 x 8.00

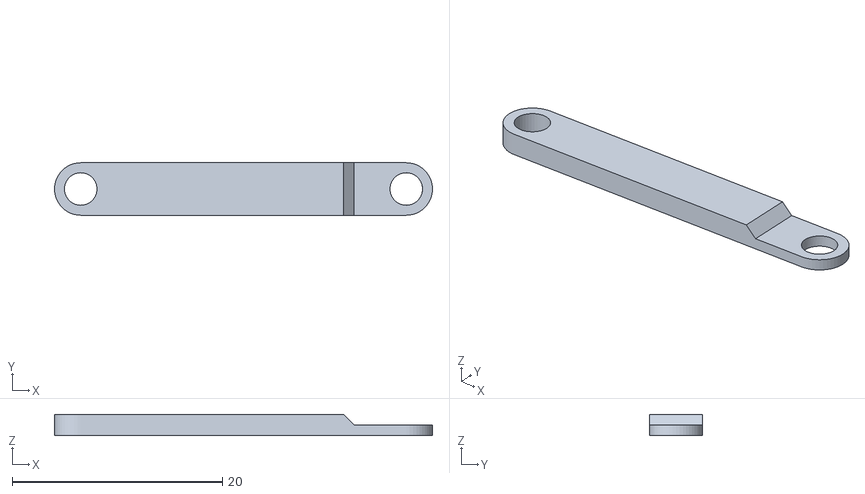
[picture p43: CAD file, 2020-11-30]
CAD/Vorderachse-Lenkstange-2x.stl
36.0 x 5.00 x 2.00

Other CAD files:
CAD/Felgen-front-2x.stl
CAD/Controller-Halterung-breadboard-1x.stl
CAD/chassis-1x.stl

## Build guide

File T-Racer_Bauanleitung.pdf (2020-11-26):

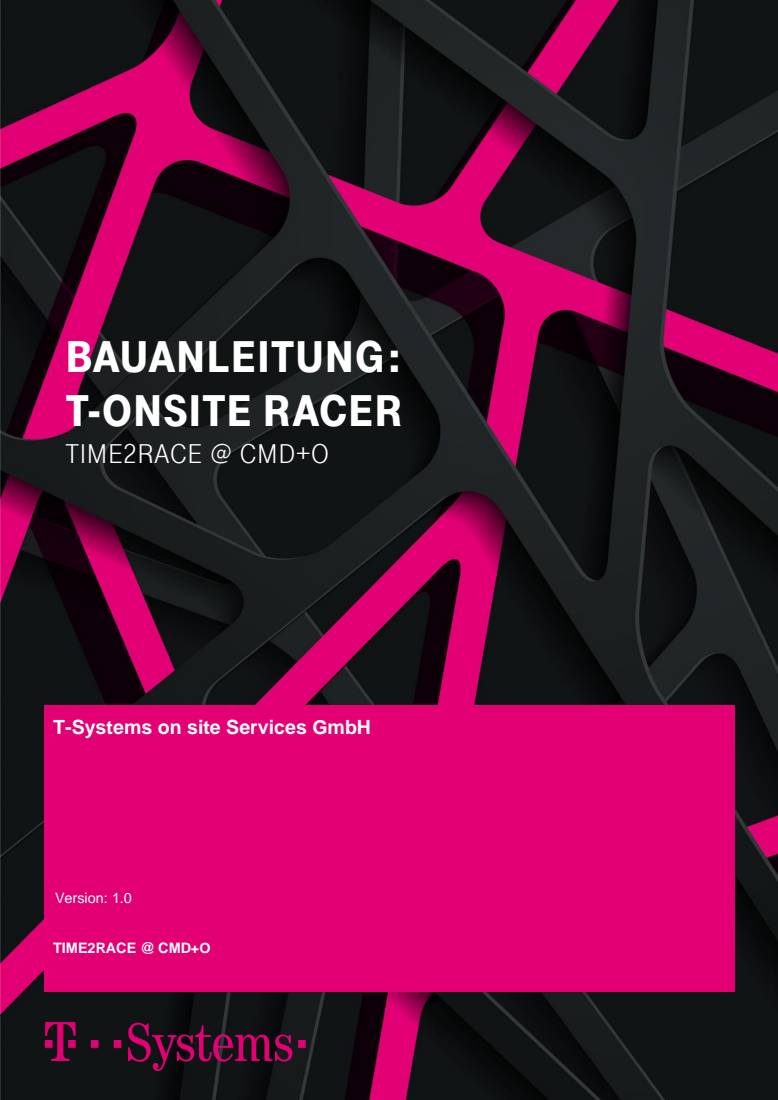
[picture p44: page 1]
BAUANLEITUNG: T-ONSITE RACER; TIME2RACE @ CMD+O; Version: 1.0

T-Systems on site Services GmbH

T-SYSTEMS ON SITE SERVICES GMBH | Seite 2 von 9
InnovationLab T-Systems onsite West | Version:1.0

Bauanleitung

## IMPRESSUM

Tabelle 1 Impressum

Herausgeber | T-Systems onsite Services GmbH
| Fasanenweg 5
| 70771 Leinfelden-Echterdingen
Version | Letztes Review | Status
1.00 | 20.11.2020

Kurzbeschreibung

Anleitung zum zusammenbauen der 3D-Druck Komponenten des T-Racers.

Copyright © 20.11.2020 by T-Systems on site Services GmbH

Alle Rechte, auch die des auszugsweisen Nachdrucks, der fotomechanischen Wiedergabe (einschließlich Mikrokopie) sowie der Auswertung durch Datenbanken oder ähnliche Einrichtungen, vorbehalten.

1 | CHECKLISTE T-RACER
Bezeichnung | Anzahl | Bild
A | 2x
B | 1x
C | 2x
D | 2x
E | 2x
E2 | 2x
F | 2x
G | 2x
H | 2x
I | 1x

J | 1x
K | 2x
K2 | 2x
L | 1x
M | 1x
N | 1x

Schrauben und Mutter

Bezeichnung | Anzahl
5mm | 4x
10mm | 16x
20mm | 2x
Muttern | 4x

2 | BAUANLEITUNG T-RACER
1. Teil A hat drei Löcher. Schraube in jedes Teil A jeweils 2 10mm Schrauben. Eine davon in das einzelne Loch und eine in das hintere Loch der nebeneinander liegenden Löcher.
Achtung: Es gibt eine linke und eine rechte Seite!

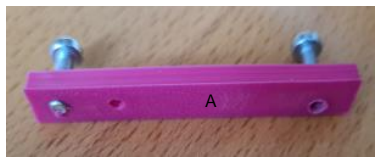
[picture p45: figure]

2. Schraube die beiden Teile A an Teil B. Hierzu verwendest du die bereits hineingeschraubten 10mm Schrauben von Teil A.

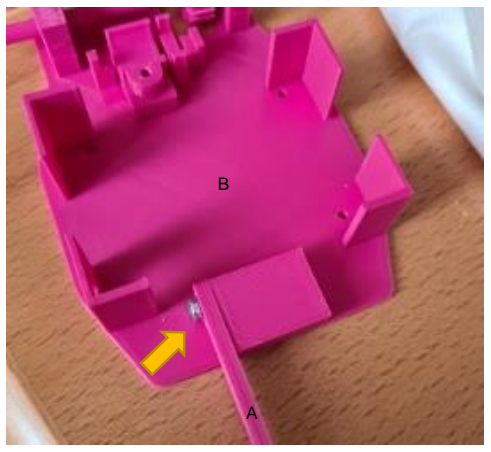
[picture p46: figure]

3. Setze nun Teil L zwischen die beiden angeschraubten Teile A und befestige diese mit den Schrauben im vorderen der beiden vorhanden Löchern. (Wenn du die Servo jetzt schon einbaust ist es einfacher das Kabel zu verlegen )

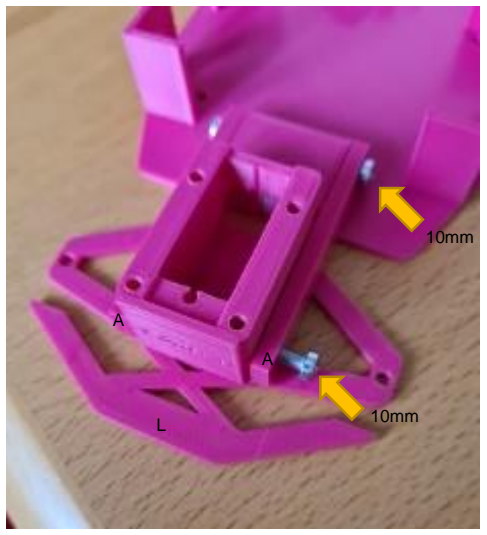
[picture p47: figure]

4. Schraube in jedes Teil E eine 20mm Schrauben bis zum Anschlag.

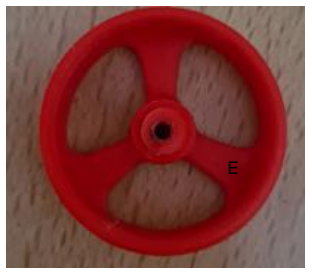
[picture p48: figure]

5. Setze in die beiden Teile H je ein Teil K. VORSICHT! Teil H hat eine linke und eine rechte Seite. Bitte beim Zusammenbauen beachten. Nimm eine 5mm Schraube und befestige, von unten, Teil H an dem bereits festgeschraubten Teil L. Teil H muss dabei mit der Öffnung nach vorne und die Nase nach hinten zeigen. Bevor du die Schraube ganz hineindrehst, setze Teil E mit der 20mm Schrauben von außen auf Teil H (Schraube durch das Kugellager).

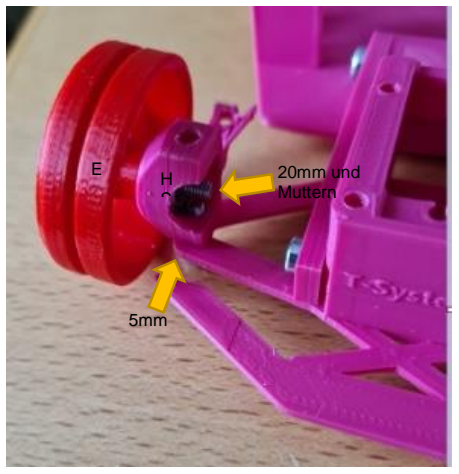
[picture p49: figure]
20mm und Muttern

6. Nimm zwei Muttern schraube diese auf die 20mm Schrauben und befestige diese (kontern). Nun kannst du die bereits hineingedrehte 5mm Schraube von unten weiter reindrehen (Teil H). Beachte, dass die Schraube nicht ganz fest gedreht werden darf. Ansonsten bewegt sich das Vorderrad nicht mehr. Probiere es einfach aus, wie weit du diese hineindrehen kannst, damit das Rad noch beweglich ist
7. Wiederhole Schritt 5 und 6 auch auf der jeweils anderen Seite (links und rechts). Hast du beide Seiten fertiggestellt, sollte dein T-Racer wie folgt aussehen.

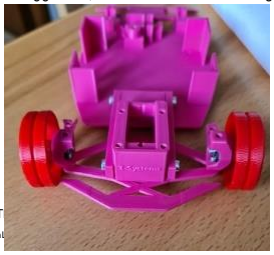
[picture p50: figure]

8. Nimm Teil G und schraube zwei 10mm Schrauben und eine 5mm Schraube in die folgenden Löcher. Beachte, dass die jeweiligen Schrauben im richtigen Loch sein müssen.

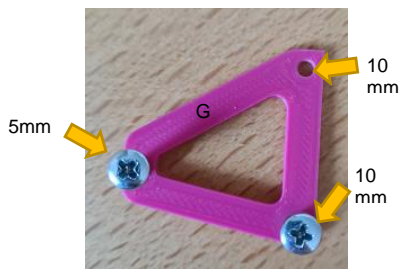
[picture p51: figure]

9. Nimm Teil G und lege es auf Teil L und Teil H. Die bereits befestigte 5mm Schrauben schraubst du in Teil H und die bereits befestigten 10mm in Teil L. Wenn alles stimmt, kommst du deinem eignen fertigen T-Racer immer näher.

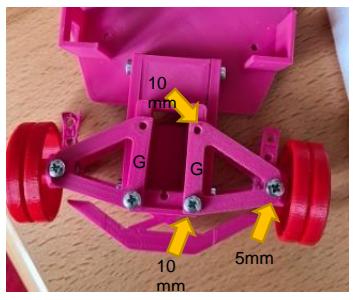
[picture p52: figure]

10. Befestige nun Teil F an Teil H. Auch hier bitte beachten, dass es eine linke und eine rechte Seite gibt. Diese sind durch „L“ und „R“ gekennzeichnet. Zum Befestigen benötigst du pro Seite zwei 10mm Schrauben, welche du durch beide Löcher drehst. Achte darauf, dass die Kennzeichnungen „L“ und „R“ dabei nach oben zeigen.
11. Schraube nun an der dicken Seite in jedes Teil C eine 10mm Schraube hinein. Beachte hierbei, dass du die Schraube in ein Teil C von oben schraubst, sodass die geriffelte Oberfläche die obere Seite darstellt. Die andere Schraube bitte so hineinschrauben, dass die glattere Oberfläche die obere Seite darstellt.

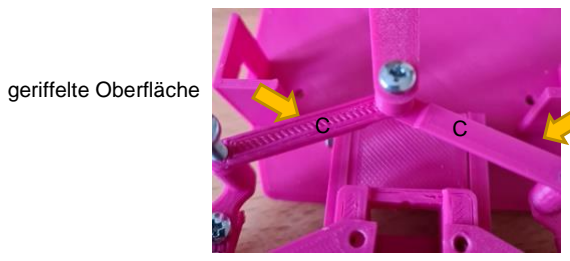
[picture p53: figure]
geriffelte Oberfläche

glattere Oberfläche

H

F

12. Nun befestige beide Teile C an den bereits verschraubten Teilen F.

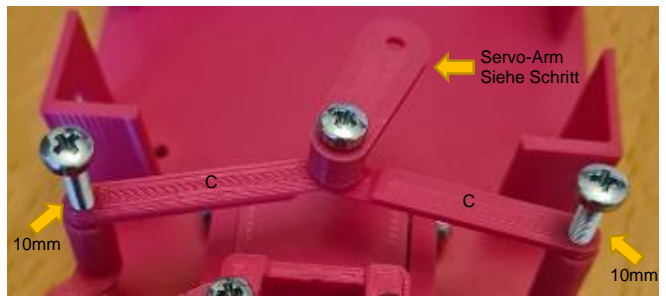
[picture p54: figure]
Servo-Arm Siehe Schritt

13. Lege nun die beiden dünnen Löcher der Teile C übereinander und befestige daran Teil I mit einer 10mm Schraube. Die Schraube drehst du in die schmalere Seite von Teil I.
Fertig ist deine Vorderachse!

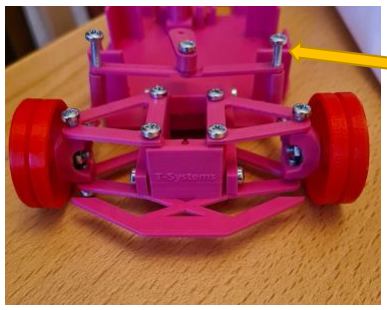
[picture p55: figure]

14. Für die Hinterachse benötigst du Teil E2, Teil K2, Teil M und N, beide Teile D und Teil J.
15. Setze Teil N so auf Teil M, dass es auf dem vorgesehenen Viereck sitzt. Stecke nun je ein Teil K2 auf jeder Seite bis es nicht mehr weitergeht. Befestige durch darauf stecken die Teile E2.

E

K

M

N

J | D

Nicht verwirren lassen! Die stehen bei euch nicht raus. Wir haben hier 20mm verwendet

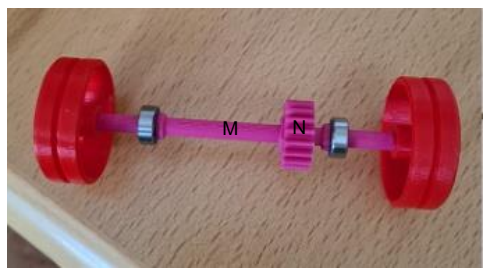
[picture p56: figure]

16. Verbinde nun das Gesamte mit deinem restlichen T-Racer. Hierzu legst du das erbaute Teil in die Vorrichtungen des Racers. Stecke nun VORSICHTIG! die beiden Teile D über das Kugellager und drücke es fest.
17. Zum Schluss befestigst du mit einer 10mm Schraube Teil J an der Motorhalterung. Die Zahnräder sollten dann perfekt ineinander greifen

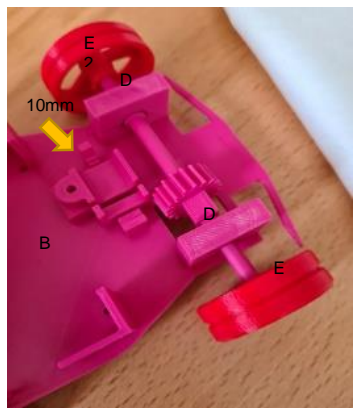
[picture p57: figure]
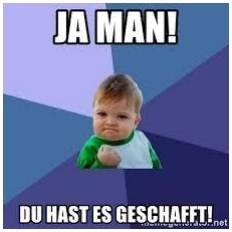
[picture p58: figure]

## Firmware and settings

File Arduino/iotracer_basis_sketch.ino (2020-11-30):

#include <ESP32Servo.h>
#include <analogWrite.h>
#include <BLEDevice.h>
#include <BLEUtils.h>
#include <BLEServer.h>

//BLE
#define SERVICE_UUID        "ae975c80-05f0-11ea-8d71-362b9e155667"
#define COMMAND_CHAR_UUID   "b81f189c-05f0-11ea-8d71-362b9e155667"

//servo parameters
Servo servo1;
static const int servoPin = 4;

//motor parameters
int motorDir = 18;
int motorPWM = 5;
 
void setup()
{
  Serial.begin(115200);
  pinMode(motorDir,OUTPUT);
  pinMode(motorPWM,OUTPUT);

  // Initialize Bluetooth Low Energy
  initBLE();

  //attach servo
  ESP32PWM::allocateTimer(0);
  ESP32PWM::allocateTimer(1);
  ESP32PWM::allocateTimer(2);
  ESP32PWM::allocateTimer(3);
  servo1.setPeriodHertz(50);    // standard 50 hz servo
  servo1.attach(servoPin);
  
  //straight forward
  servo1.write(90);
  //stop motor
  stopMotor();
  
}
 
void loop()
{

}


void motorPower(int fb) { //value from 0 to 255, 128 to stop motor
    if(fb == 128)
      stopMotor();
    else if(fb > 128)
      moveForward(fb);
    else
      moveBackwards(fb);
}


void stopMotor() {
  //stop motor
}

void moveForward(int fb) {
 //move forwards
}

void moveBackwards(int fb) {
  //move backwards
}

void steer (int steer){
//servo
  
}


void carControl(int steer, int pow) { 
      //steer
      //motorPower
}

void initBLE() {
  //define ble T-Racer Profile and start advertising
}

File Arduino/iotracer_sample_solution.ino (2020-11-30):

#include <ESP32Servo.h>
#include <analogWrite.h>
#include <BLEDevice.h>
#include <BLEUtils.h>
#include <BLEServer.h>

//BLE
#define SERVICE_UUID        "ae975c80-05f0-11ea-8d71-362b9e155667"
#define COMMAND_CHAR_UUID   "b81f189c-05f0-11ea-8d71-362b9e155667"
BLEDevice           Device;
BLEServer*          pServer;
BLEService*         pService;
BLECharacteristic*  pControllCharacteristic;
BLEAdvertising*     pAdvertising;

//servo parameters
Servo servo1;
int pos = 0; 
//static const int servoPin = 25;
static const int servoPin = 4;

//motor pins (just for test method)
int INA = 18;
//int INA = 13;
int INB = 5;

//motor Pins
int motorDir = 18;
//int motorDir = 13;
int motorPWM = 5;
 
void setup()
{
  Serial.begin(115200);
  pinMode(motorDir,OUTPUT);
  pinMode(motorPWM,OUTPUT);

  // Initialize Bluetooth Low Energy
  initBLE();
  
  ESP32PWM::allocateTimer(0);
  ESP32PWM::allocateTimer(1);
  ESP32PWM::allocateTimer(2);
  ESP32PWM::allocateTimer(3);
  servo1.setPeriodHertz(50);    // standard 50 hz servo
  servo1.attach(servoPin, 1000, 2000);
  servo1.write(90);
  stopMotor();
}
 
void loop()
{

/*  for(int posDegrees = 0; posDegrees <= 180; posDegrees++) {
        carControl(posDegrees, 255);
        Serial.println(posDegrees);
        delay(100);
  }

  for(int posDegrees = 180; posDegrees >= 0; posDegrees--) {
        carControl(posDegrees, 0);
        Serial.println(posDegrees);
        delay(100);
   }
   */
}

void motorPower(int fb) { //value from 0 to 255, 128 to stop motor
    if(fb == 128)
      stopMotor();
    else if(fb > 128)
      moveForward(fb);
    else
      moveBackwards(fb);
}

void stopMotor() {
  digitalWrite( motorDir, LOW ); // Set motor to off
  digitalWrite( motorPWM, LOW );
}

void moveForward(int fb) {
  Serial.print("move forward - ");
  digitalWrite( motorDir, HIGH ); // direction = forward
  int pow = 255 - ((fb - 128) * 2);
  //int pow =fb;
  Serial.print("Set value to motor:  ");
  Serial.println(pow);
  analogWrite( motorPWM, pow );
}

void moveBackwards(int fb) {
  Serial.print("move backword - ");
  digitalWrite( motorDir, LOW ); // direction = backwards
  int pow = 255 - (fb * 2);
  //int pow =fb;
  Serial.print("Set value to motor:  ");
  Serial.println(pow);
  analogWrite(motorPWM, pow);
}

void carControl(int lr, int fb) {
      steer(lr);
      motorPower(fb);
}

void steer(int angle) {
  servo1.write(angle); //angle: the value to write to the servo, from 0 to 180
}

// Server Callbacks
class ServerCallbacks : public BLEServerCallbacks {
    void onConnect(BLEServer* pServerCallback) {
      Serial.println("Client connected");
    }

    void onDisconnect(BLEServer* pServerCallback) {
      Serial.println("Client disconnected");
      stopMotor();
    }
};

class CharacteristicCallbacks: public BLECharacteristicCallbacks {
    //
    void onWrite(BLECharacteristic* pCharacteristic) {
      std::string value = pCharacteristic->getValue(); //receive value via BLE from characteristic
      String svalue= value.c_str();
      Serial.println("value received:  "+svalue);
      int splitindex = svalue.indexOf(',');  //parse value(speed, steer)
      int speed = svalue.substring(0,splitindex).toInt(); //get spped value
      int steer = svalue.substring(splitindex+1).toInt(); //get steer valu
      carControl(steer, speed); //send values to motors
    }
};

void initBLE() {

  Device.init("IoT_Racer"); //Give your Device a custom name (Bluetooth-Name)
  pServer       = Device.createServer();
  pService      = pServer->createService(SERVICE_UUID);
  pControllCharacteristic  = pService->createCharacteristic(COMMAND_CHAR_UUID, BLECharacteristic::PROPERTY_WRITE_NR | BLECharacteristic::PROPERTY_READ | BLECharacteristic::PROPERTY_WRITE); //set write property to characteristic so that we can write values to it
  // has to be enabled for iOS
  pControllCharacteristic->setWriteNoResponseProperty(true);


  Device.setEncryptionLevel(ESP_BLE_SEC_ENCRYPT);
  pControllCharacteristic->setAccessPermissions(ESP_GATT_PERM_READ_ENCRYPTED | ESP_GATT_PERM_WRITE_ENCRYPTED);

  //define callbacks
  pServer->setCallbacks(new ServerCallbacks());
  pControllCharacteristic->setCallbacks(new CharacteristicCallbacks());


  pControllCharacteristic->setValue("128,90"); //set value to 128,90 -> motor off

  pService->start();

  //Start Advertising
  pAdvertising = Device.getAdvertising();
  pAdvertising->addServiceUUID(SERVICE_UUID);
  pAdvertising->setScanResponse(true);
  pAdvertising->setMinPreferred(0x06);
  pAdvertising->setMinPreferred(0x12);
  Device.startAdvertising();
  Serial.println("Start Advertising");
}

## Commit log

2020-11-30 add CAD Files, add app source code, update implementation guide, add smaple solution
2020-11-30 - update CAD Files
    [Controller-Halterung-breadboard-1x.stl, Felgen-front-2x.stl, Felgen_heck-2x.stl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]
2020-12-01 update "tuning" wirediagram
